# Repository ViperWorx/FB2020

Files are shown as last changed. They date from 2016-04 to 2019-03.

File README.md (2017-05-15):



<h3>Reliability, Speed, Accuracy, Open Source</h3>

This sums up the FB2020 CoreXY 3D Printer. We use these printers ourselves and wouldn’t sell the kits if we didn’t think they were up to snuff. Our FB2020s have run thousands of hours with very little down time. We print all the FB2020 printed parts on our FB2020s.

<h3>Reliability</h3>

The FB2020’s heart is the tried and trusted RAMPS 1.4 & Arduino Mega running the Marlin Firmware. It has tried and trusted A4988 Stepper Drivers moving the motors . With an AxMod 3D Print Drakon Geared extruder powering the filament through the bowden tube into a Genuine E3D v6 Hot end. This makes for a winning combination. The heated bed is a glass sheet heated by the tried and trusted Mk2B PCB heater. All of this adds up to a reliable printer.

<h3>Speed</h3>

With the 32 bit upgrade, replacing the Arduino Mega for a Re-Arm 32 Bit controller running Smoothieware, the FB2020 can handle 150mm/s speeds without skipping a beat. The standard Arduino Mega, being 8 bit, can handle speeds up to 80mm/s

<h3>Low Maintenance Accuracy</h3>

Running the E3D v6 and the Drakon Geared Extruder, it’s smooth printing. The FB2020 is capable of layer heights of 60 Microns up to 500 Microns and can print pretty much any filament you can throw at it. Adding a sheet of Printbite with the Basic bed upgrade allows for a low maintenance bed with great adhesion. The Full bed upgrade uses the same Printbite sheet on top of a laser cut 6061 5mm thick Aluminium bed heated by a SSR switched Mains heater. This speeds heat up times and allows bed temperatures of up to 130°c.  Upgrading the Drakon Extruder to a SLS version gives even more piece of mind for smooth running.

The Bill of Materials and further infomation can be found in the Wiki.

Firmware can be found at https://github.com/AxMod3DPrint/FB2020-Firmware

<hr />
<table border="0px">
<th align="left">
&copy; AxMod 3D Print 2017.
</th>
<tr>
<td>
This documentation describes Open Hardware and is licensed under the CERN OHL v. 1.2.
</td>
</tr>
<tr>
<td>
You may redistribute and modify this documentation under the terms of the
CERN OHL v.1.2. (http://ohwr.org/cernohl). This documentation is distributed
WITHOUT ANY EXPRESS OR IMPLIED WARRANTY, INCLUDING OF
MERCHANTABILITY, SATISFACTORY QUALITY AND FITNESS FOR A
PARTICULAR PURPOSE. Please see the CERN OHL v.1.2 for applicable
conditions
</td>
</tr>
</table>

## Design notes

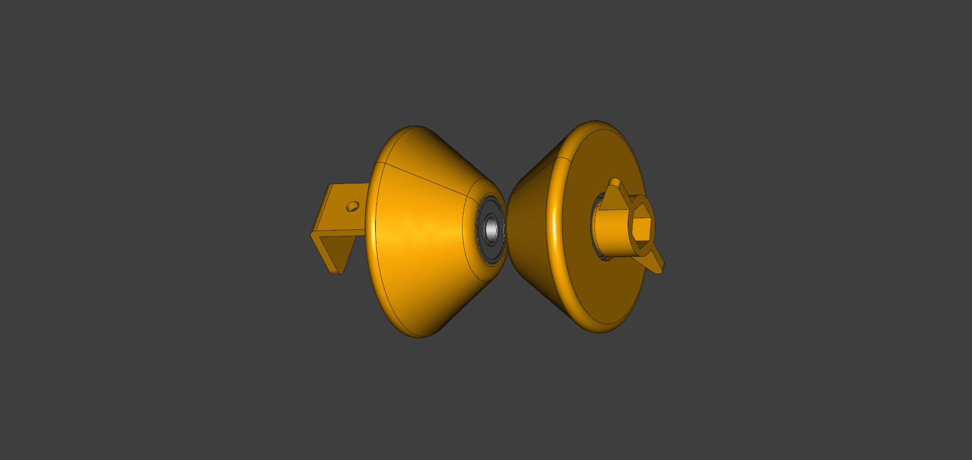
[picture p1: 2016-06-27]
Images/Spool Clamp_1.png

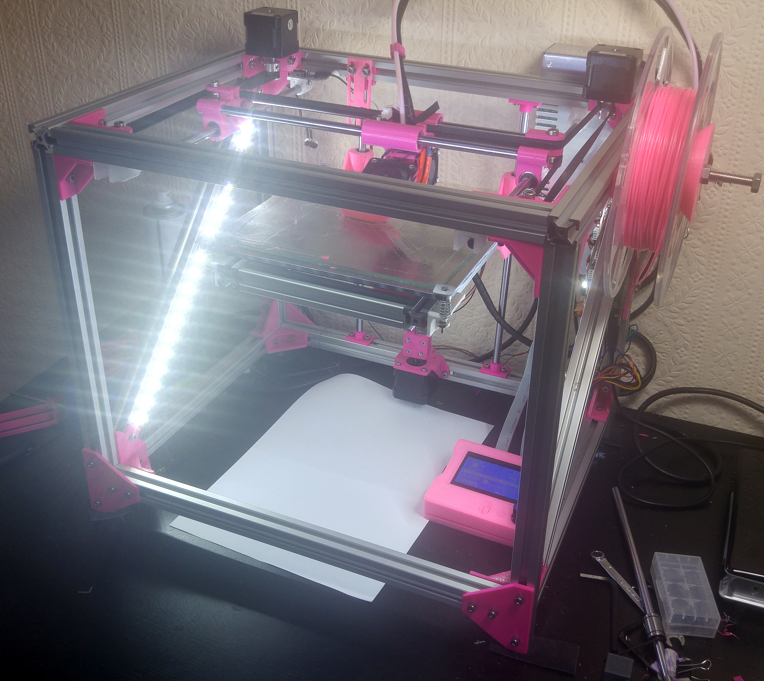
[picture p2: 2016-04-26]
Images/20160318_093008_HDR.jpg

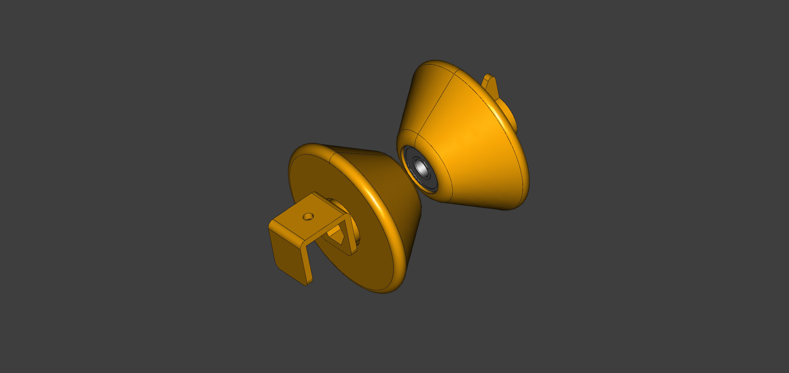
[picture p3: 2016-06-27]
Images/Spool Clamp_2.png

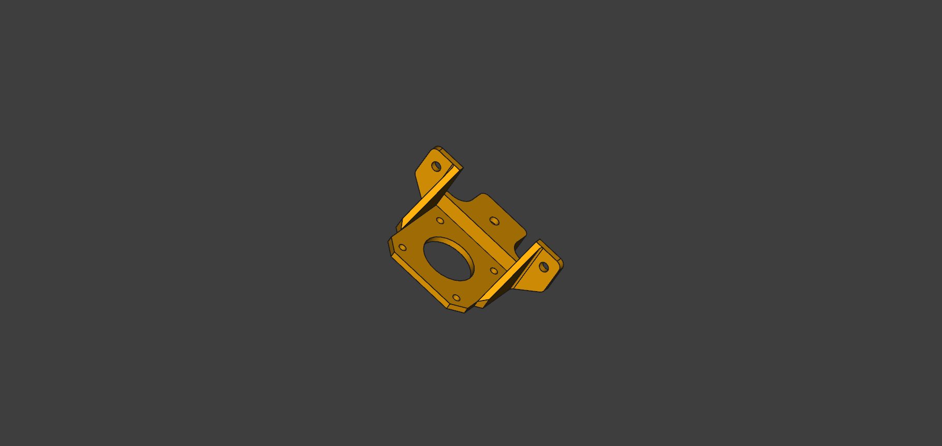
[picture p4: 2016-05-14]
Images/Z_Motor_Holder_1.png

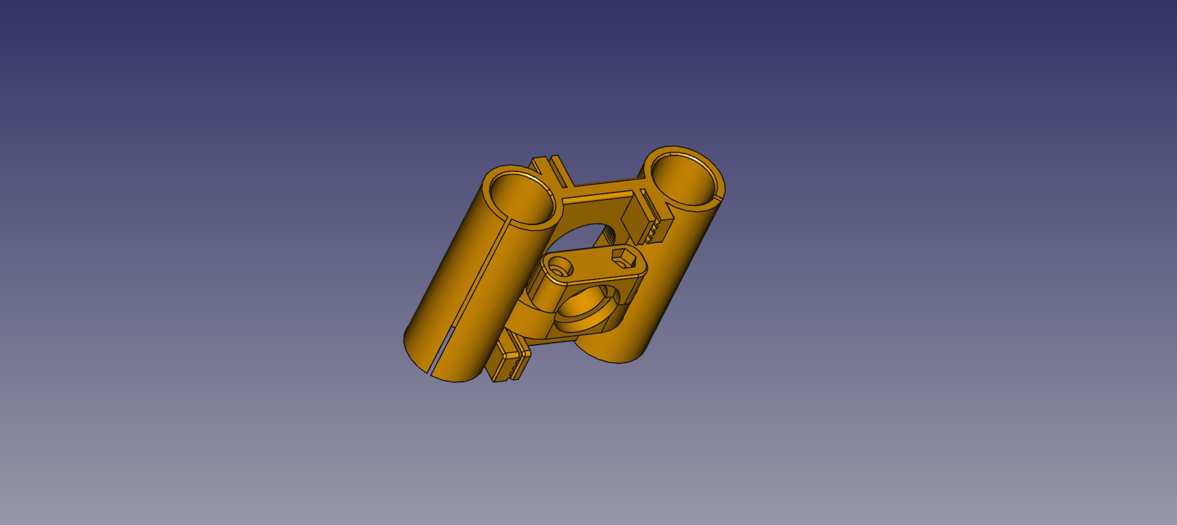
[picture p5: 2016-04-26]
Images/1_Carriage_freecad.png

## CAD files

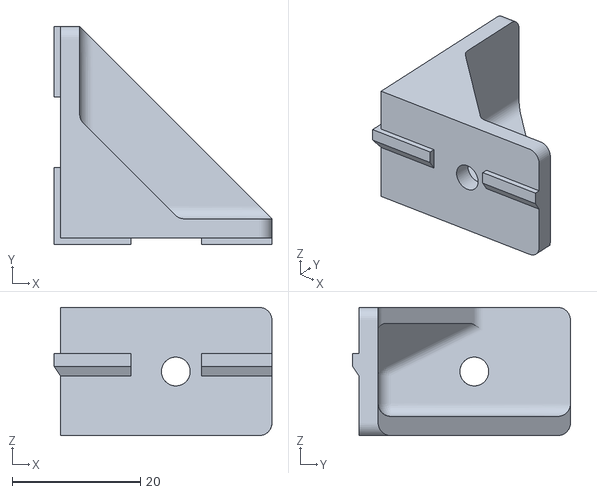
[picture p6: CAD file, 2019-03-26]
12_Corner_Bracket.stl
34.0 x 34.0 x 20.0

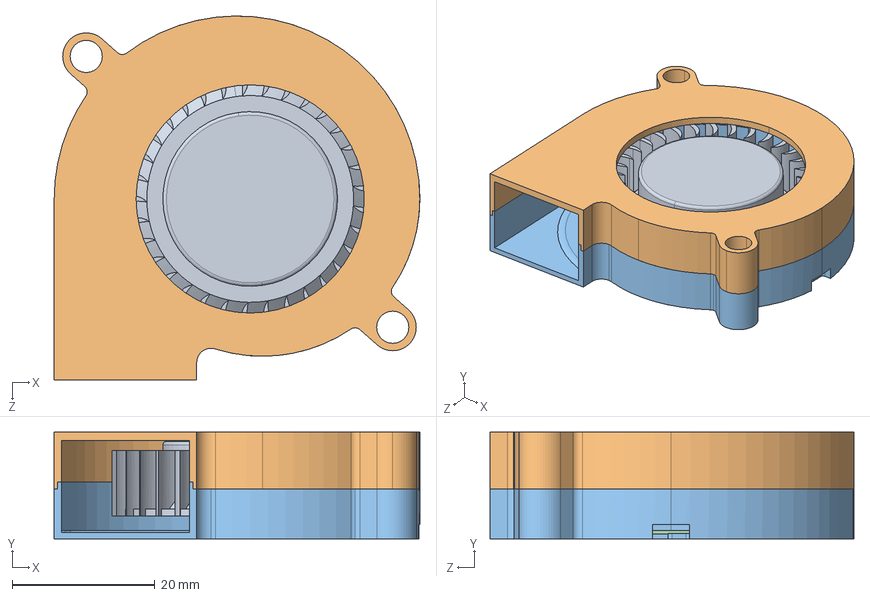
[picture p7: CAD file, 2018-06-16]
FreeCad/CAD Files/Radial-Cooling-Fan-5015-DC12V.STEP
51.3 x 15.0 x 51.1 mm
turbine
top
bottom

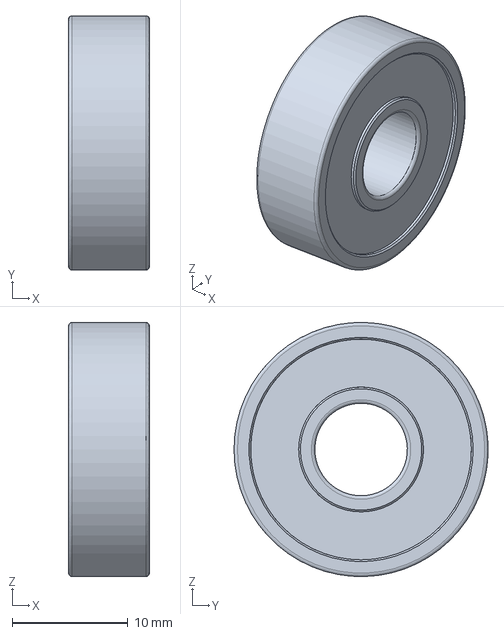
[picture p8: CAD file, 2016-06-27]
FreeCad/IGES/608ZZ.igs
7.00 x 22.0 x 22.0 mm

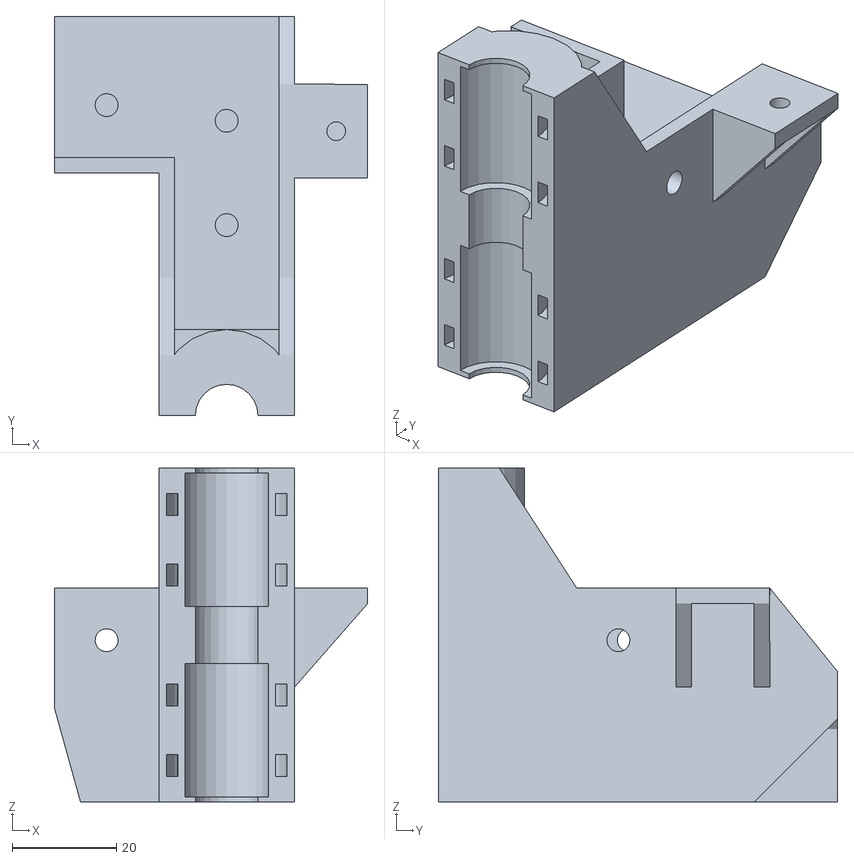
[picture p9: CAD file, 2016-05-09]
SCAD/Left_Bed_Holder_NEW.stl
60.0 x 76.5 x 64.0

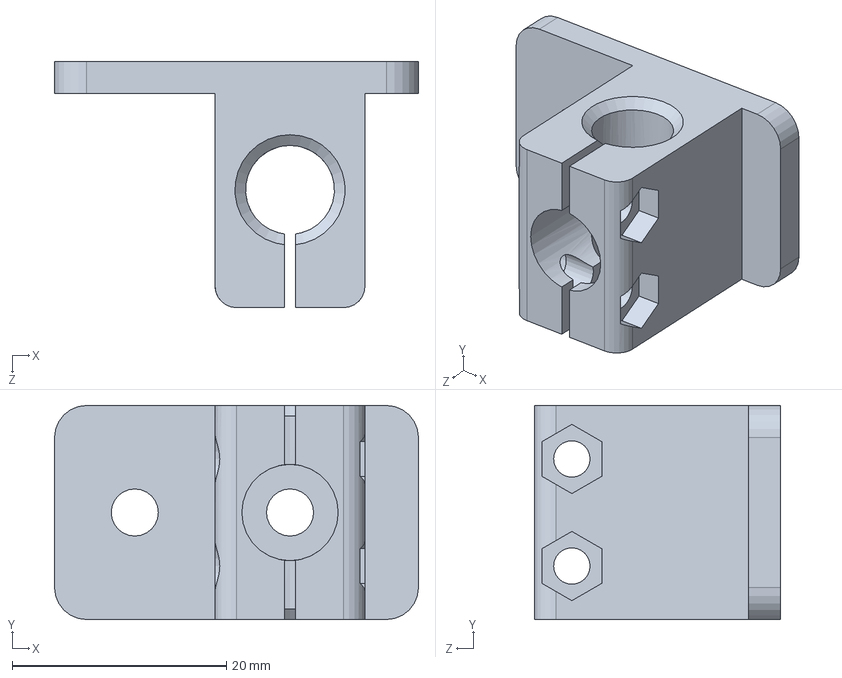
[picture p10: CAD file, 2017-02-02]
Solidworks/SW-2_Y_Rod_Holder_Left.SLDPRT
34.0 x 20.0 x 23.0 mm

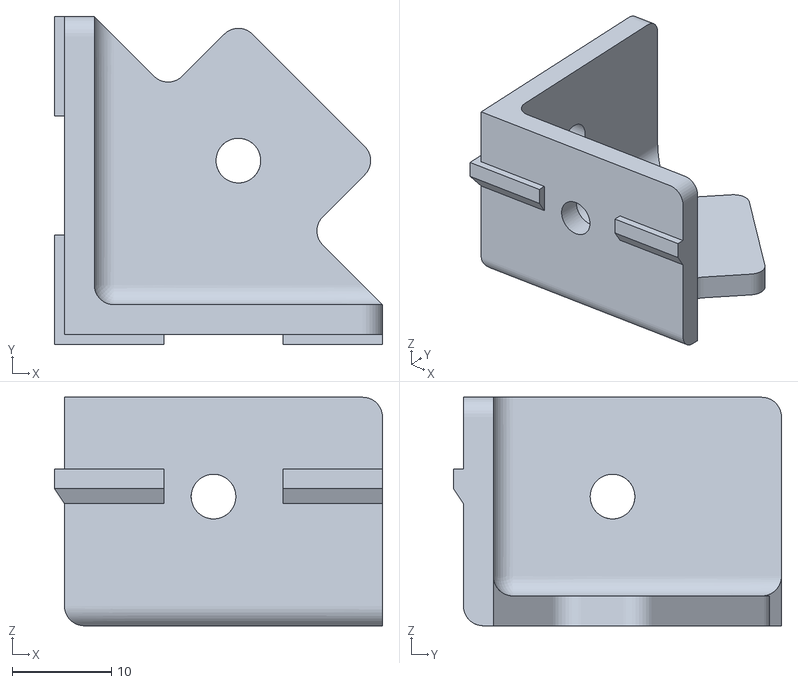
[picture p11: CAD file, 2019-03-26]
4_Corner_Brace_Mount.stl
33.0 x 33.0 x 23.0

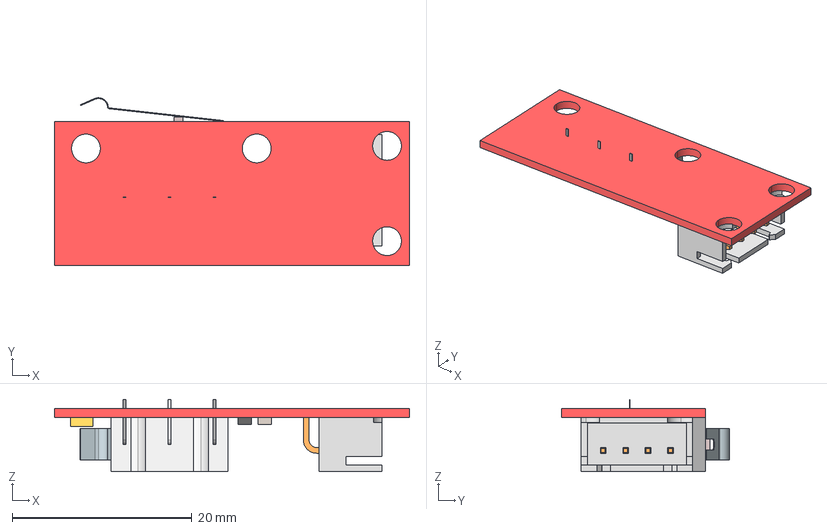
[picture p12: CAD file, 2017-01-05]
FreeCad/CAD Files/Endstop2.stp
39.5 x 18.6 x 8.02 mm
PCB Geometry
PCB^Endstop
Microswitch_1A_125vAC(seul)
JST 4Pin

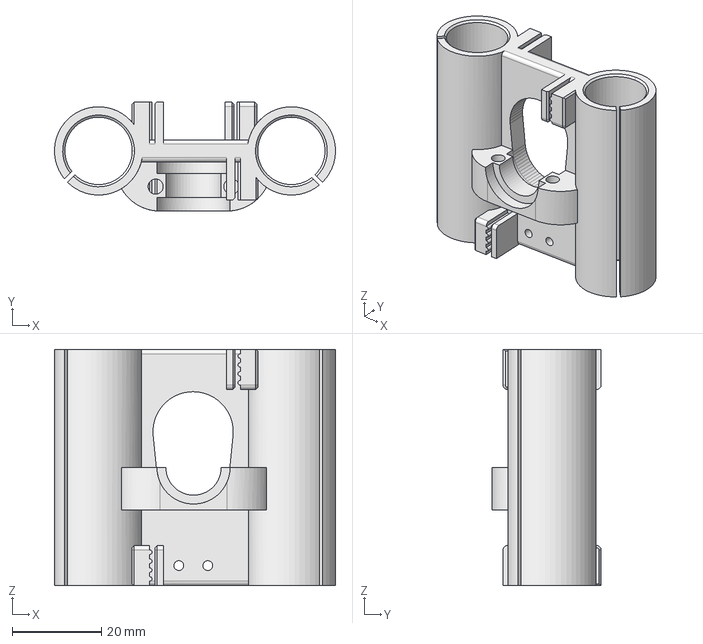
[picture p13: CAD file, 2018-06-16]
FreeCad/FB2020_Carriage.step
63.0 x 24.5 x 53.0 mm

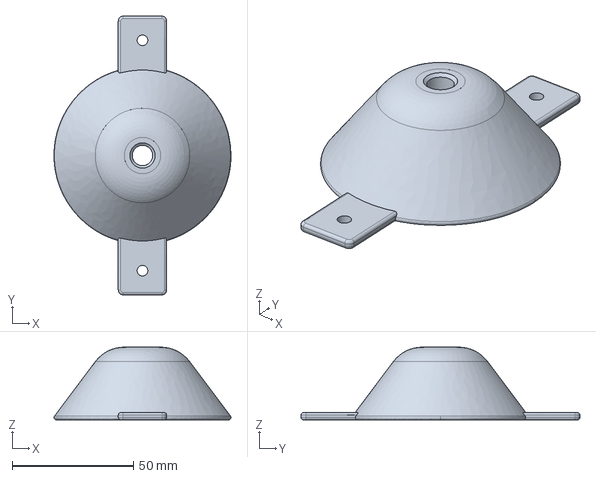
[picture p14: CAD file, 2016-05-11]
FreeCad/IGES/Spool_Clamp_Frame.iges
73.0 x 115.0 x 30.0 mm

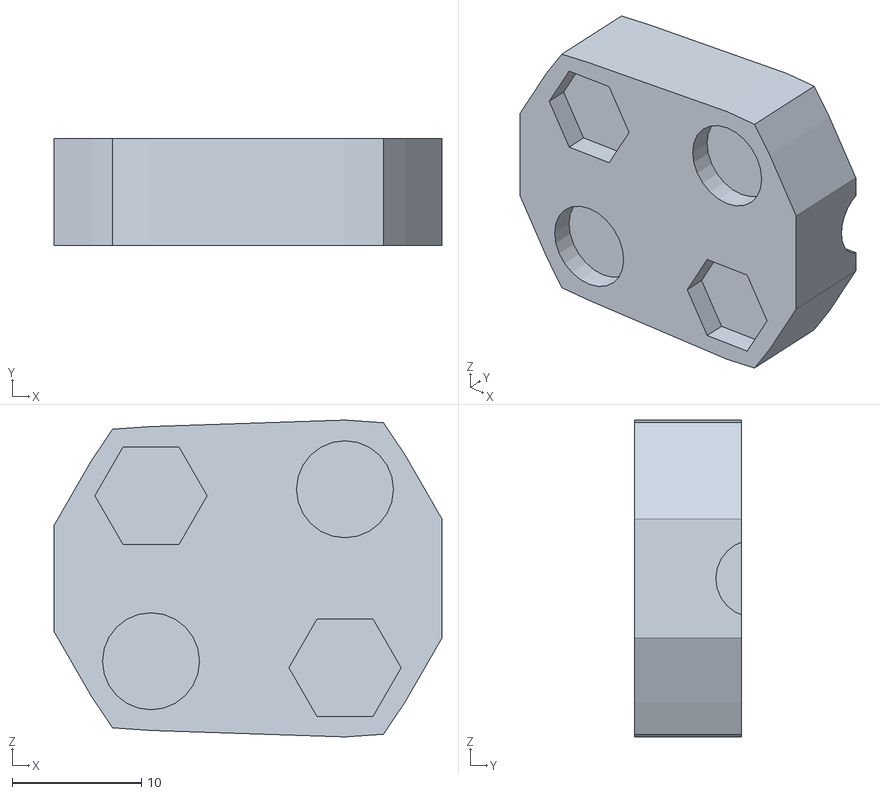
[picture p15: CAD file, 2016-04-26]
SCAD/coupler.stl
30.0 x 8.30 x 24.5

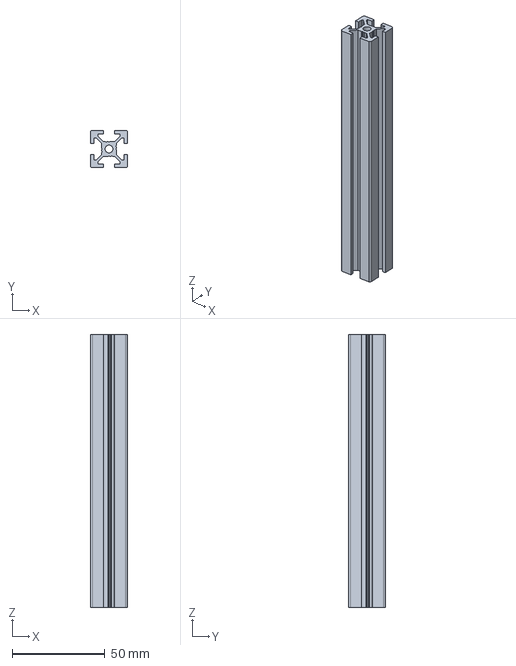
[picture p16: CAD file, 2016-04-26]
FreeCad/CAD Files/NFS5-2020-147_2_03.stp
20.0 x 20.0 x 147.0 mm

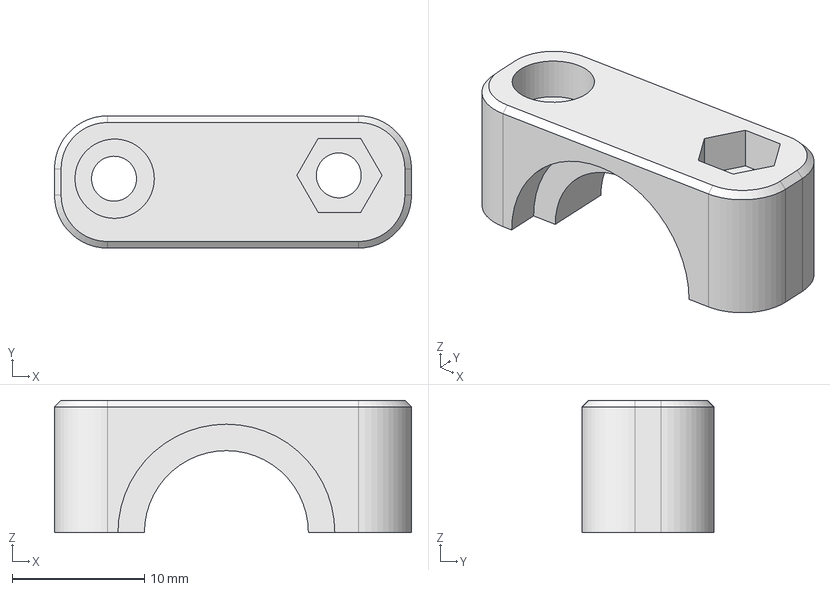
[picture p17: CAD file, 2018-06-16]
FreeCad/FB2020_Carriage_Clamp.step
27.0 x 10.0 x 10.0 mm

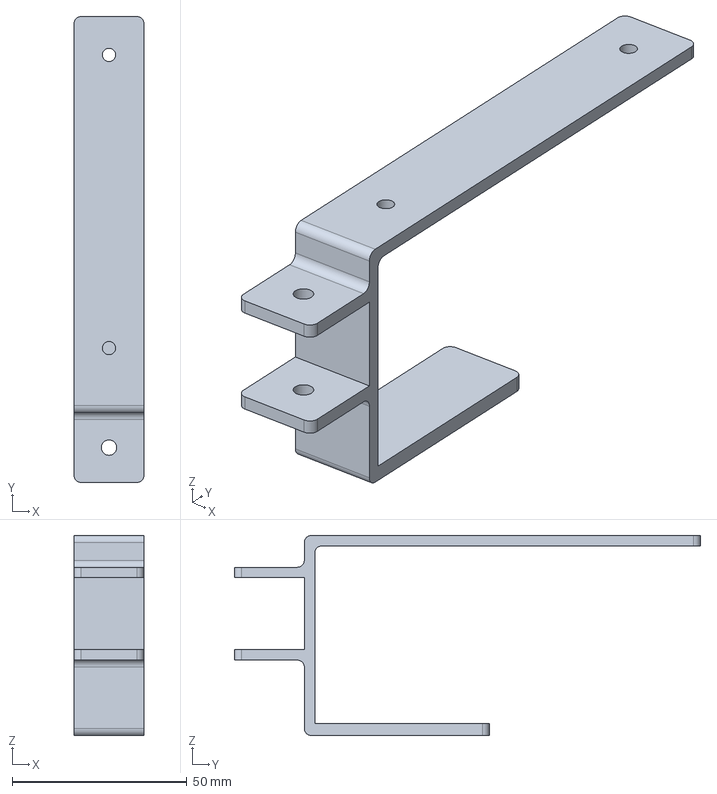
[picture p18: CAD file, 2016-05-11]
FreeCad/IGES/PSU_Mount_2.iges
20.0 x 133.5 x 57.3 mm

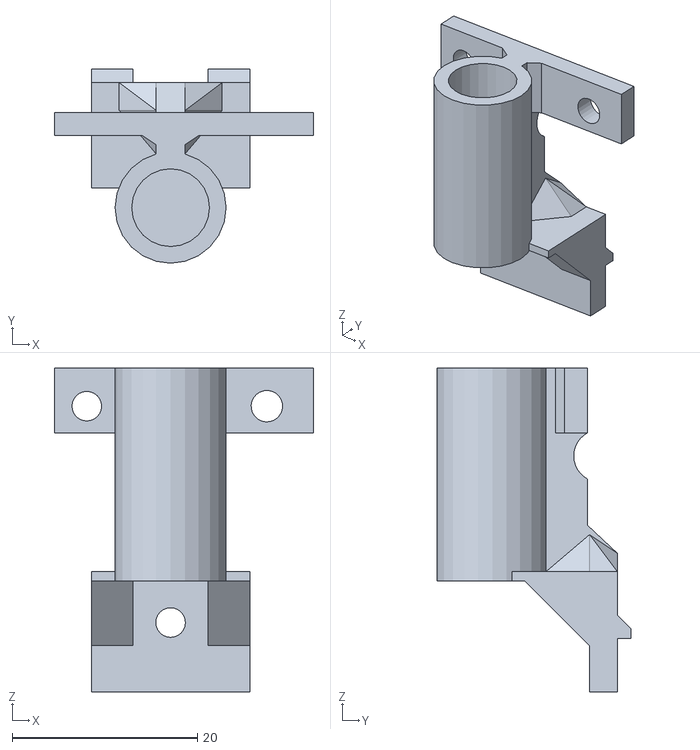
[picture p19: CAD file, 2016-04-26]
SCAD/rod_clamp_endstop.stl
28.0 x 21.0 x 35.0

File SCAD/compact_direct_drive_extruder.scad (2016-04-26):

// Compact direct drive bowden extruder for 1.75mm filament
// Licence: CC BY-SA 3.0, http://creativecommons.org/licenses/by-sa/3.0/
// Author: Dominik Scholz <schlotzz@schlotzz.com> and contributors
// Using MK8 style hobbed pulley 13x8mm from: https://www.reprapsource.com/en/show/6889
// visit: http://www.schlotzz.com
// changed: 2014-04-04, added idler slot and funnel on bowden side for easier filament insertion
// changed: 2014-04-27, placed base and idler "printer ready"
// changed: 2014-09-22, fixed non-manifold vertexes between base and filament tunnel
// changed: 2014-11-13, added bowden inlet
// changed: 2015-03-17, updated idler for better MK7 drive gear support
// changed: 2015-10-13, designed alternative idler to solve breaking of bearing support


/*
	design goals:
	- use 13x8mm hobbed pulley (mk8) or 13x12mm (mk7)
	- filament diameter parametric (1.75mm or 3mm)
	- use 608zz bearing
	- use M5 push fit connector
*/

// avoid openscad artefacts in preview
epsilon = 0.01;

// increase this if your slicer or printer make holes too tight
extra_radius = 0.2;

// major diameter of metric 3mm thread
m3_major = 2.85;
m3_radius = m3_major / 2 + extra_radius;
m3_wide_radius = m3_major / 2 + extra_radius + 0.2;

// diameter of metric 3mm hexnut screw head
m3_head_radius = 3 + extra_radius;

// drive gear
drive_gear_outer_radius = 8.00 / 2;
drive_gear_hobbed_radius = 7 / 2;
drive_gear_hobbed_offset = 3.5;
drive_gear_length = 13.5;
drive_gear_tooth_depth = 0.5;

// base width for frame plate
base_width = 20;
base_length = 62;
base_height = 5;

// nema 17 dimensions
nema17_width = 42.3;
nema17_hole_offsets = [
	[-15.5, -15.5, 1.5],
	[-15.5,  15.5, 1.5],
	[ 15.5, -15.5, 1.5],
	[ 15.5,  15.5, 1.5 + base_height]
];

// inlet type
inlet_type = 0; // 0:normal, 1:push-fit


// filament
filament_diameter = 1.75; // 1.75, 3.00
filament_offset = [
	drive_gear_hobbed_radius + filament_diameter / 2 - drive_gear_tooth_depth,
	0,
	base_height + drive_gear_length - drive_gear_hobbed_offset - 2.5
];





// helper function to render a rounded slot
module rounded_slot(r = 1, h = 1, l = 0, center = false)
{
	hull()
	{
		translate([0, -l / 2, 0])
			cylinder(r = r, h = h, center = center);
		translate([0, l / 2, 0])
			cylinder(r = r, h = h, center = center);
	}
}


// mounting plate for nema 17
module nema17_mount()
{
	// settings
	width = nema17_width;
	height = base_height;
	edge_radius = 27;
	axle_radius = drive_gear_outer_radius + 1 + extra_radius;

	difference()
	{
		// base plate
		translate([0, 0, height / 2])
			intersection()
			{
				cube([width, width, height], center = true);
				cylinder(r = edge_radius, h = height + 2 * epsilon, $fn = 128, center = true);
			}
		
		// center hole
		translate([0, 0, -epsilon]	)
			cylinder(r = 11.25 + extra_radius, h = base_height + 2 * epsilon, $fn = 32);

		// axle hole
		translate([0, 0, -epsilon])
			cylinder(r = axle_radius, h = height + 2 * epsilon, $fn = 32);

		// mounting holes
		for (a = nema17_hole_offsets)
			translate(a)
			{
				cylinder(r = m3_radius, h = height * 4, center = true, $fn = 16);
				cylinder(r = m3_head_radius, h = height + epsilon, $fn = 16);
			}
	}
}


// plate for mounting extruder on frame
module frame_mount()
{
	// settings
	width = base_width;
	length = base_length;
	height = base_height;
	hole_offsets = [
		[0,  length / 2 - 6, 2.5],
		[0, -length / 2 + 6, 2.5]
	];
	corner_radius = 3;

	difference()
	{
		// base plate
		intersection()
		{
			union()
			{
				translate([0, 0, height / 2])
					cube([width, length, height], center = true);
				translate([base_width / 2 - base_height / 2 - corner_radius / 2, 0, height + corner_radius / 2])
					cube([base_height + corner_radius, nema17_width, corner_radius], center = true);
				translate([base_width / 2 - base_height / 2, 0, 6])
					cube([base_height, nema17_width, 12], center = true);
			}

			cylinder(r = base_length / 2, h = 100, $fn = 32);
		}

		// rounded corner
		translate([base_width / 2 - base_height - corner_radius, 0, height + corner_radius])
			rotate([90, 0, 0])
				cylinder(r = corner_radius, h = nema17_width + 2 * epsilon, center = true, $fn = 32);

		// mounting holes
		for (a = hole_offsets)
			translate(a)
			{
				cylinder(r = m3_wide_radius, h = height * 2 + 2 * epsilon, center = true, $fn = 16);
				cylinder(r = m3_head_radius, h = height + epsilon, $fn = 16);
			}

		// nema17 mounting holes
		translate([base_width / 2, 0, nema17_width / 2 + base_height])
			rotate([0, -90, 0])
			for (a = nema17_hole_offsets)
				translate(a)
				{
					cylinder(r = m3_radius, h = height * 4, center = true, $fn = 16);
					cylinder(r = m3_head_radius, h = height + epsilon, $fn = 16);
				}
	}
}


// inlet for filament
module filament_tunnel()
{
	// settings
	width = 9;
	length = nema17_width;
	height = filament_offset[2] - base_height + 4.5;

	translate([0, 0, height / 2])
	{
		difference()
		{
			union()
			{
				// base
				translate([-height / 2, 0, 0])
					cube([width + height, length, height], center = true);

				// inlet strengthening
				translate([0, -length / 2, -height / 2 + filament_offset[2] - base_height])
					rotate([90, 0, 0])
						cylinder(r = 3.5, h = 1, center = true, $fn = 32);

				// outlet strengthening
				translate([0, length / 2, -height / 2 + filament_offset[2] - base_height])
					rotate([90, 0, 0])
						cylinder(r = 4.5, h = 1, center = true, $fn = 32);

				// idler tensioner
				intersection()
				{
					translate([5, -length / 2 + 8, 0])
						cube([width, 16, height], center = true);
					translate([-17.8, -20 ,0])
						cylinder(r = 26.5, h = height + 2 * epsilon, center = true, $fn = 32);
				}

			}

			// middle cutout for drive gear
			translate([-filament_offset[0], 0, 0])
				cylinder(r = 11.25 + extra_radius, h = height + 2 * epsilon, center = true, $fn = 32);

			// middle cutout for idler
			translate([11 + filament_diameter / 2, 0, 0])
				cylinder(r = 12.5, h = height + 2 * epsilon, center = true, $fn = 32);

			// idler mounting hexnut
			translate([filament_diameter + 1, -nema17_width / 2 + 4, .25])
				rotate([0, 90, 0])
					cylinder(r = m3_radius, h = 50, center = false, $fn = 32);
			translate([filament_diameter + 3, -nema17_width / 2 + 4, 5])
				cube([2.5 + 3 * extra_radius, 5.5 + 2.5 * extra_radius, 10], center = true);
			translate([filament_diameter + 3, -nema17_width / 2 + 4, 0])
				rotate([0, 90, 0])
					cylinder(r = 3.15 + 2.5 * extra_radius, h = 2.5 + 3 * extra_radius, center = true, $fn = 6);
			
			// rounded corner
			translate([-height - width / 2, 0, height / 2])
				rotate([90, 0, 0])
					cylinder(r = height, h = length + 2 * epsilon, center = true, $fn = 32);
			
			// funnnel inlet
			if (inlet_type == 0)
			{
				// normal type
				translate([0, -length / 2 + 1 - epsilon, -height / 2 + filament_offset[2] - base_height])
					rotate([90, 0, 0])
						cylinder(r1 = filament_diameter / 2, r2 = filament_diameter / 2 + 1 + epsilon / 1.554,
							h = 3 + epsilon, center = true, $fn = 16);
			}
			else
			{
				// inlet push fit connector m5 hole
				translate([0, -length / 2 - 1 + 2.5 + epsilon, -height / 2 + filament_offset[2] - base_height])
					rotate([90, 0, 0])
						cylinder(r = 2.25, h = 5 + 2 * epsilon, center = true, $fn = 16);

				// funnel inlet outside
				translate([0, -length / 2 + 4, -height / 2 + filament_offset[2] - base_height])
					rotate([90, 0, 0])
						cylinder(r1 = filament_diameter / 2, r2 = filament_diameter / 2 + 1,
							h = 2, center = true, $fn = 16);

			}

			// funnnel outlet inside
			translate([0, 12, -height / 2 + filament_offset[2] - base_height])
				rotate([90, 0, 0])
					cylinder(r1 = filament_diameter / 2, r2 = filament_diameter / 2 + 1.25,
						h = 8, center = true, $fn = 16);

			// outlet push fit connector m6 hole
			translate([0, length / 2 + 1 - 2.5 + epsilon, -height / 2 + filament_offset[2] - base_height])
				rotate([90, 0, 0])
					cylinder(r = 2.8, h = 5 + 2 * epsilon, center = true, $fn = 16);

			// funnel outlet outside
			translate([0, length / 2 - 4, -height / 2 + filament_offset[2] - base_height])
				rotate([90, 0, 0])
					cylinder(r1 = filament_diameter / 2 + 1, r2 = filament_diameter / 2,
						h = 2, center = true, $fn = 16);

			// filament path
			translate([0, 0, -height / 2 + filament_offset[2] - base_height])
				rotate([90, 0, 0])
					cylinder(r = filament_diameter / 2 + 2 * extra_radius,
						h = length + 2 * epsilon, center = true, $fn = 16);
			
			// screw head inlet
			translate(nema17_hole_offsets[2] - [filament_offset[0], 0, height / 2 + 1.5])
				sphere(r = m3_head_radius, $fn = 16);
		}
	}
}


// render drive gear
module drive_gear()
{
	r = drive_gear_outer_radius - drive_gear_hobbed_radius;
	rotate_extrude(convexity = 10)
	{
		difference()
		{
			square([drive_gear_outer_radius, drive_gear_length]);
			translate([drive_gear_hobbed_radius + r, drive_gear_length - drive_gear_hobbed_offset])
				circle(r = r, $fn = 16);
		}
	}
}
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

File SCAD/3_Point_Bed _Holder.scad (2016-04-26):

$fn=64;
difference(){
cube([40,20,3]);
translate([8,10,-1])
cylinder(d=4.2,h=5);
translate([35,10,-1])
cylinder(d=4.2,h=5);
}
difference(){
cube([40,3,15]);
translate([20.5,4,10.5])
rotate([90,0,0])
cylinder(d=3.4,h=5);
}
difference(){
cube([3,20,15]);
translate([-1,2,16])
rotate(a=34, v=[-1,0,0])
cube([5,25,20]);
}


difference(){
translate([40,0,0])
cube([3,20,15]);
translate([39,2,16.05])
rotate(a=34, v=[-1,0,0])
cube([5,25,20]);
}

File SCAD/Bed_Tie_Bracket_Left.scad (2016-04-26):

$fn=64;



module stiffening(){
translate([2.5,2.5,0])
cylinder(d=5, h=35);
translate([0,2.5,2.5])
rotate([0,90,0])
cylinder(d=5, h=26);
translate([2.5,0,2.5])
rotate([-90,0,0])
cylinder(d=5, h=20);
}

difference(){
cube([26,20,3]);
translate([13,10,-1])
cylinder(d=4.4, h=5);
}


difference(){
cube([3,20,35]);
translate([-1,10,10])
rotate([0,90,0])
cylinder(d=4.4, h=5);
translate([-1,10,28])
rotate([0,90,0])
cylinder(d=4.4, h=5);
}
difference(){
cube([26,3,35]);
translate([26,-1,5])
rotate([0,-35,0])
cube([20,5,50]);
}
stiffening();

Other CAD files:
Solidworks/SW-2_Y_Rod_Holder_Right.SLDPRT
Solidworks/SW-1_RRD_Case_Button.SLDPRT
1_Carriage_E3D_Threaded_Heatsink.stl
FreeCad/CAD Files/NFS5-2020-340_2_03.stp
SCAD/Bed _Holder.scad
1_12mm_Bed_Carrier_Left.stl
1_12mm_Bed_Carrier_Right.stl
1_30mm_Fan_Guard.stl
1_3_Point_Bed _Holder.stl
1_Bed_Tie_Bracket_Left.stl
1_Bed_Tie_Bracket_Right.stl
1_Bowden_Clip.stl
1_Carriage.stl
1_Carriage_clamp.stl
1_Carrier_Left.stl
1_Carrier_Right.stl
1_Compact_Direct_Drive_Extruder.stl
1_E3D_duct_small.stl
1_Extruder_Spring_Holder.stl
1_Left_Bed_Holder_Clamp_Short.stl
1_Left_Bed_Holder_clamp.stl
1_Left_Idler_Corner.stl
1_MKS_Base_Mount.stl
1_PSU_Mount_1_S-200-12.stl
1_PSU_Mount_2_S-200-12.stl
1_RAMPS_Box_Base.stl
1_RAMPS_Box_Lid.stl
1_RAMPS_Box_Reset_Button.stl
1_RAMPS_Mount.stl
1_RRD_Case Front.stl
1_RRD_Case_Back.stl
1_RRD_Case_Button.stl
1_RRD_Knob.stl
1_RRD_Knob_15mm.stl
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

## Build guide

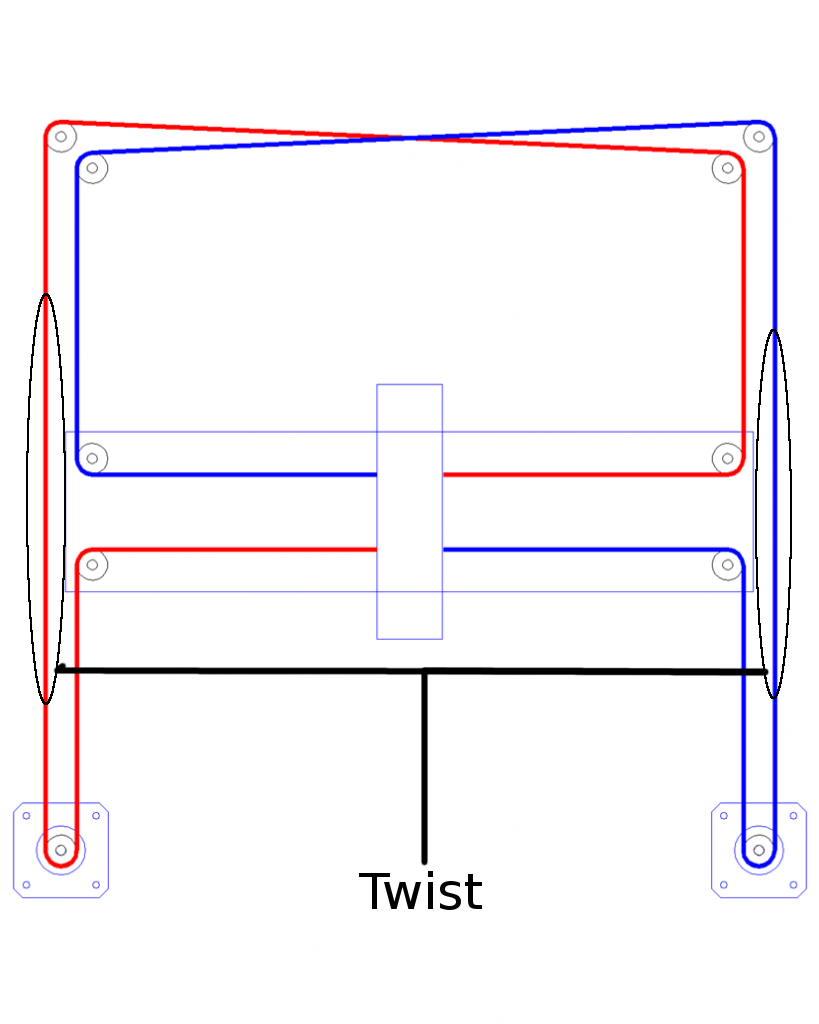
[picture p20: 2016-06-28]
Build Guide/Images/Belt Path2.png

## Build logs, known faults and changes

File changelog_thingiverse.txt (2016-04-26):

#####02/02/16

original upload

#####03/02/16

Bed Mounts uploaded

#####04/02/16

Rigid coupler added

#####05/02/16

Rigid Coupler design slimmed down (damn my spacial awareness), Carriage modified to stiffen up clamp for E3D

#####06/02/16

Carriage modified to allow for printing without supports, clamp shortened by 2mm

#####07/02/16

Bed Holder bearing holes enlarged by 0.3mm to allow easier fitting of the bearings and to allow for printing variances. Carriage SCAD file & RAMPS mount uploaded

#####09/02/16

Modified Z Leadscrew Holder & Z Endstop mount - original had holes too close for T nuts.

#####14/02/15

Added quick and dirty spool clamp. Needs M8 Threaded rod and 2 13mm nuts

#####16/02/15

Added carriers for Y axis. Designed to work with the new X Carriage as the belt clips will not align with the existing Carriers. Uploaded all parts. Carriers printed and found to be a little tight on the bearings and not enough space to guide the belts. Modified to guide the belts, left carrier now has endstop lug to hit the Y endstop.

#####18/02/15

Reinforced Y rod carriers, fed up of them breaking. Carrier near right hand idler will need support. Printed and modified again (removed cap our rail mounts) to allow for irregular length rods. Mine are ~1mm out. Carriers modified to allow the same. Bill of Materials added

#####20/02/15

Carriage modified, reinforcing belt clips fixed bearing alignment with carriers. Bed Carrier extrusion slots widened by 0.4mm. Far too tight to fit the bed extrusions effectively.

#####25/02/15

Left and Right Carriers now have inbuilt support on the clamp slot, this was done due to printing issues. Extruder Carriage now has slightly thicker and taller belt clips. Spool holder nut slot enlarged due to being too small. Short version of the Z axis Carriers added, allows use of LM8LUUs. Removed rigid coupler as there's a slight Z wobble. Leadscrew nut holder central hole increased in size as too small. All files refreshed and have been numbered with the amount to print. Lost spool holder SCAD file in a shift-delete accident.. :(. Files marked Culain are originals from Culain's design. The bed holders have just been re-orientated and mirrored, no other physical changes have been made. After a conversation over on the RepRap forums, the option to add an endstop to the Extruder Carriage has been added. You will need a standard Omron style micro-switch and 2x 14mm M2 bolts, these should screw directly into the Carriage but can alst use nuts on the other side. This allows one bundle of cables and tubing to be moving over having the endstop moving on the Y Axis and the Bowden tube moving on the Carriage. Derped on hole placement for Omron Microswitch, corrected. Moved Y endstop bumper down, wouldn't make proper contact. Uploaded SCAD files for Carriers and Spool Clamp, didn't delete it after all.

#####27/02/16

Added Left carrier with no endstop mount to complement the move of the endstop to the carriage - this will print without support, STL & SCAD file uploaded for this. Updated RAMPS mount, Derped putting stand-offs on the wrong side. Moved the RAMPS in by 5mm

#####03/03/16

Front Bed Holders reworked as they did not fit. Corner Idlers strengthened, the top bearing holder was constantly breaking on the right side. Z Endstop mount lengthened due to not enough travel. Renamed FB2020 due to very little being left of the original design and is now in it's own right a different printer. Added Bowden Tube wire clips, source added.

#####06/03/16

Z Endstop reworked, now uses an Omron-style limit switch and bumps off of the Z Carrier. Fron Bed Tie added to stiffen up bed, (this can be changed out for another 147mm Extrusion piece and 2 more corner brackets. Front bed holders tweaked to bring holes in line with the Z Axis bed holders. Added a new Rigid Coupler for the Z Axis, clamps concentrically with 2x M3x16 Bolts. Z Leadscrew length shortened to 250mm as 300mm fouls the Extruder carriage

#####08/03/15

Carriage - Belt clip notches moved to opposite side and E3D mount widened to allow easy fitting - SCAD file modified to allow extra diameter for printing. A twist in the Belts on the outer long runs is now needed. This makes the belt run on the smooth side for all the idlers and increases print quality.

Idlers - Re-orientated for strength layers are now in the opposite direction of the belt tension, now need printing with support.

Bowden tube wire clips added to keep Bowden tube and hot end wiring together and tidy

Bowden Clip added to keep E3D collet up and stop filament backlash.

Compact Direct Drive Extruder added - modified for a 6mm Pneumatic Coupler and an E3D HobbGoblin Drive Gear

Updated BOM to reflect changes.

#####02/04/16

Firmware updated to Marlin 1.1 RC4. Enabled Mesh Bed Levelling and PID on the Bed. X0 Y0 is the Front left of the printer, Y homes to Max.

#####07/04/16

Changed layer fan for spinorkit's 2 pronged setup, which has been shortened to allow clearance of the leadscrew, this layer fan assembly is a lot more effective as it cools from two sides. As such this needed a new Active cooling duct for the E3D hot end, to mount the layer fan off of, this cooling duct clamps with 2 22mm M3 bolts and will not move once clamped.

#####14/04/16

Description updated and planned changes added.

#####17/04/16

Bed converted to 3 point levelling, new brackets added, use front bed tie for the middle of the bed to stiffen. Longer lengths for bed reduced to 235mm.

#####19/04/16

Carriage updated. Added extra room for cabling from hot end & flattened off clamp on carriage. This should allow for easier belt fitting and will retain the nut on the clamp on the carriage. Several minor changes including centring up of the hot end. Note the STLS are uploaded with 0.4mm tolerance as my Prusas print tight. If you need less grab the SCAD file.

#####20/04/16

Carriage extended by 5mm to allow further easier fitting of belts and hot end. There's roughly 4.5mm either side of the bed so there is room for further extension if needed.

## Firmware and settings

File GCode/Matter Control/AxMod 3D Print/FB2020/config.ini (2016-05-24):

avoid_crossing_perimeters = 1
bed_shape = rectangular
bed_size = 200,200
bed_temperature = 60
bottom_clip_amount = 0
bridge_acceleration = 0
bridge_fan_speed = 100
bridge_flow_ratio = 1
bridge_speed = 20
brim_width = 0
build_height = 170
cancel_gcode = 
center_part_on_bed = 1
complete_objects = 0
cool_extruder_lift = 0
cooling = 1
create_raft = 0
default_acceleration = 0
disable_fan_first_layers = 1
end_gcode = M140 S0 T0; set bed temperature to 0\nM104 S0 T0; set extruder temperature to 0\nM107 ; disable fan\nG91 ;Relative positioning\nG1 E-1 F300  ;retract the filament a bit before lifting the nozzle to release some of the pressure\nG1 E-5 F4800; Retract\nG90 ; Absolute positioning\nG1 Z275; Bed to bottom of printer\nG28 X Y F4800; home X & Y axis\nM84; disable all stepper motors\nM117 Work Complete!end_gcode = M140 S0 T0; set bed temperature to 0\nM104 S0 T0; set extruder temperature to 0\nM107 ; disable fan\nG91 ;Relative positioning\nG1 E-1 F300  ;retract the filament a bit before lifting the nozzle to release some of the pressure\nG1 E-5 F4800; Retract\nG90 ; Absolute positioning\nG1 Z275; Bed to bottom of printer\nG28 X Y F4800; home X & Y axis\nM84; disable all stepper motors\nM117 Work Complete!
external_perimeter_speed = 50%
external_perimeters_first = 0
extra_perimeters = 1
extruder_clearance_height = 20
extruder_clearance_radius = 20
extruder_count = 1
extruder_offset = 0x0,0x0,0x0,0x0
extruders_share_temperature = 0
extrusion_axis = E
extrusion_multiplier = 1
extrusion_width = 0
fan_always_on = 0
fan_below_layer_time = 60
filament_diameter = 1.75
fill_angle = 45
fill_density = 30%
fill_pattern = honeycomb
first_layer_acceleration = 0
first_layer_bed_temperature = 75
first_layer_height = 90%
first_layer_speed = 30%
first_layer_temperature = 205
g0 = 0
gap_fill_speed = 20
gcode_arcs = 0
gcode_comments = 0
gcode_flavor = reprap
gcode_output_type = REPRAP
has_fan = 1
has_hardware_leveling = 0
has_heated_bed = 1
has_sd_card_reader = 1
heat_extruder_before_homing = 0
infill_acceleration = 0
infill_every_layers = 1
infill_extruder = 1
infill_extrusion_width = 0
infill_first = 0
infill_only_where_needed = 0
infill_overlap_perimeter = .06
infill_speed = 50
infill_type = GRID
layer_gcode = 
layer_height = 0.2
max_fan_speed = 100
min_extrusion_before_retract = .1
min_fan_speed = 35
min_print_speed = 10
min_skirt_length = 0
notes = 
nozzle_diameter = 0.4
only_retract_when_crossing_perimeters = 1
ooze_prevention = 0
output_filename_format = [input_filename_base].gcode
overhangs = 1
pause_gcode = 
perimeter_acceleration = 0
perimeter_extruder = 1
perimeter_extrusion_width = 0
perimeter_speed = 30
perimeters = 3
post_process = 
print_center = 100,100
raft_air_gap = .2
raft_extruder = 0
raft_extra_distance_around_part = 5
raft_fan_speed_percent = 100
raft_layers = 0
raft_print_speed = 100%
randomize_start = 0
repair_outlines_extensive_stitching = 0
repair_outlines_keep_open = 0
resolution = 0
resume_gcode = 
retract_before_travel = 20
retract_layer_change = 1
retract_length = 6.4
retract_length_tool_change = 10
retract_lift = 0.2
retract_restart_extra = 0
retract_restart_extra_toolchange = 0
retract_speed = 30
skirt_distance = 6
skirt_height = 1
skirts = 3
slowdown_below_layer_time = 30
small_perimeter_speed = 30
solid_fill_pattern = rectilinear
solid_infill_below_area = 70
solid_infill_every_layers = 0
solid_infill_extrusion_width = 0
solid_infill_speed = 60
spiral_vase = 0
standby_temperature_delta = -5
start_gcode = G21 ; mm\nG90; Absolute Pos\nM107; Fan off\nG28; home all\nG92 E0 ;Zero Extruder\nG1 Z0.3 ;Move Z to 0.3mm to avoid scraping bed\nG1 X100 Y5 F4000 ;Move to half way along front edge of the bed\nG1 Z0.05 ;Move Nozzle close to bed\nG1 E10 F90 ; Extrude 10mm \nG1 X20 F120000; move to X20 as fast as firmware permits\nG1 Z2 ; Lift nozzle to 2mm ready to start main sequence\nG92 E0 ;Zero Extruder
start_perimeters_at_concave_points = 0
start_perimeters_at_non_overhang = 0
support_material = 0
support_material_angle = 45
support_material_enforce_layers = 0
support_material_extruder = 1
support_material_extrusion_width = 0
support_material_infill_angle = 45
support_material_interface_extruder = 1
support_material_interface_layers = 3
support_material_interface_spacing = 0
support_material_pattern = honeycomb
support_material_spacing = 2.5
support_material_speed = 50
support_material_threshold = 0
support_material_xy_distance = 0.7
support_material_z_distance = 0.15
support_material_z_gap_layers = 1
support_type = LINES
temperature = 200
thin_walls = 1
threads = 2
toolchange_gcode = 
top_infill_extrusion_width = 0
top_solid_infill_speed = 50
top_solid_layers = 3
travel_speed = 110
use_firmware_retraction = 0
use_relative_e_distances = 0
vibration_limit = 0
wipe = 1
wipe_shield_distance = 0
wipe_tower_size = 0
z_can_be_negative = 0
z_offset = 0

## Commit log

2016-04-26 Redesign of Z rod holder
    [4_Z_Rod_Mount.stl, Z_Rod_Holder.fcstd]
2016-04-26 mv old rod holder to old files
    [4_Z_Rod_Mount_Culain.stl]
2016-04-26 Made Z Rod Holder larger with more support around the base
    [4_Z_Rod_Mount.stl, Z_Rod_Holder.fcstd]
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2016-04-27 Full CAD design updated Filament loading GCode length reduced.
    [FB2020.fcstd]
2016-04-27 Extruder mounts converter to M4
    [1_Compact_Direct_Drive_Extruder.stl, 1_Compact_Direct_Drive_Extruder_M4.stl]
2016-04-27 printed T nuts in wrong place
    [20_M4 _T_Nut.stl]
2016-04-28 Adding mount for MKS Base board
    [1_MKS_Base_Mount.stl, MKS_Base_mount.fcstd]
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2016-04-30 Adding new images and mounts
    [1_Compact_Direct_Drive_Extruder.stl, 1_PSU_Mount_1.stl, 1_PSU_Mount_2.stl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]
2016-04-30 moved old bed holder scad file to correct folder
    [Bed_Holder.scad]
2016-04-30 PSU Mount - moved mounting point
    [1_PSU_Mount_1.stl, 1_PSU_Mount_2.stl, PSU_Mount.fcstd]
2016-05-01 removing old SCAD PSU mounts
    [PSU-A.scad, PSU-B.scad]
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2016-05-04 moving Bed standoff to test files
    [12_Corner_Bracket_Culain.stl, 1_Bed_Holder_Left.stl, 1_Bed_Holder_Right.stl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]
2016-05-04 moving to correct folder
    [Nyloc-nut-M3.step]
2016-05-04 adding FreeCAD version of foot
    [foot.fcstd]
2016-05-06 brackets in wrong folder
    [12_Corner_Bracket_Culain.stl]
2016-05-08 Carriage updated to new Freecad version
    [1_Carriage.stl, 1_Carriage_clamp.stl]
2016-05-08 Spool clamp Smoothed off for easier removal from bed
    [1_Spool_Clamp_Frame.stl, 1_Spool_Clamp_Outer.stl, Spool_Clamp.fcstd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]
2016-05-08 Foot Freecad file in wrong folder
    [foot.fcstd]
2016-05-09 adding missing reference files
    [Left_Bed_Holder_NEW.stl, left_bed_holder_clamp.scad]
2016-05-10 Adding Test files for Z Axis using 12mm rods
    [12mm_Bed_Carrier.fcstd, 12mm_Bed_Carrier_Left.stl]
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2016-05-10 RRD Mount bracket modified to work with case (to be pushed)
    [1_RRD_Mounting_Bracket_Left_FB2020.stl, 1_RRD_Mounting_Bracket_Right_FB2020.stl]
2016-05-10 slight change to model
    [1_Spool_Clamp_Frame.stl]
2016-05-10 recovery from FreeCad Crash
    [12mm_Bed_Carrier.fcstd]
2016-05-10 Adding 12mm Rod Mount Model
    [12mm_Z_Rod_Holder.fcstd]
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2016-05-10 reducing number of printed T nuts
    [10_M4_T_Nut.stl]
2016-05-10 Adding 12mm Z Rod holder
    [12mm_Z_Rod_Holder.stl]
2016-05-11 Correcting hole size on tab
    [4_Corner_Brace_Mount.stl, 4_Corner_Brace_Mount_Culain.stl]
2016-05-11 adding IGES files - request
    [12mm_Bed_Carrier.iges, 12mm_Z_Rod_Holder.iges, Carriage.iges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]
2016-05-11 Z Endstop tidied up and strengthened
    [1_Z_Endstop.stl, Z_Endstop.fcstd, Z_Endstop.iges]
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2016-05-12 Bottom Corner Brackets Re-Designed#
    [4_Alternate Bottom Bracket_Culain.stl, 4_Bottom_Corner_Bracket.stl, Bottom _Corner_Bracket.fcstd]
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2016-05-13 retiring printed coupler in favour of a rigid coupler
    [2_FB2020_Coupler.stl]
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2016-05-16 Orientating correctly
    [1_Carrier_Left.stl, 1_Carrier_Right.stl]
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2016-05-18 Removing Front Bed Tie
    part is no longer used due to 3 point levelling.
    [1_Front_Bed_Tie.stl]
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2016-05-20 Convert Z Axis to use 12mm Rods
    Z Axis now uses 12mm Smooth rods for extra stability.
    [12mm_Bed_Carrier_Left.stl, 12mm_Z_Rod_Holder.stl, 1_12mm_Bed_Carrier_Left.stl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]
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2016-05-20 Z Rod Holder - added 0.1mm Tolerance
    [12mm_Z_Rod_Holder.fcstd, 4_12mm_Z_Rod_Holder.stl]
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2016-05-23 RAMPS Enclosure Redesigned.
    Added Reset button and extra height to allow for LCD header.
    [RAMPS_Box_Base.stl, RAMPS_Box_Lid.stl, RAMPS_Box_Reset_Button.stl]
2016-05-23 Moving RAMPS box CAD to correct folder
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2016-05-24 Adding RAMPS Enclosure to main files, moved old mount to old files
    RAMPS mount now obsolete, Superseeded by the RAMPS Enclosure.
    [1_RAMPS_Box_Base.stl, 1_RAMPS_Box_Lid.stl, 1_RAMPS_Box_Reset_Button.stl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]
2016-05-24 Adding 30mm Fan Guard for E3D heatsink fan
    [1_30mm_Fan_Guard.stl, 30mm Fan Guard.fcstd]
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2016-05-24 Save from FreeCAD Crash
    [Rod_Clamp.fcstd]
2016-05-26 Y Rod Holders modified to allow for Pan head bolts - name updated
    Y Rod holders renamed from Rod_Clamp* to Rod_Holder* for clarity. Removed excess on model stopping Pan head bolts being used.
    [1_Rod_Clamp_Endstop.stl, 1_Rod_Clamp_Right_Idler.stl, 1_Rod_Holder_Endstop.stl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]
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2016-05-28 Correcting Orientation
    [1_RAMPS_Box_Base.stl]
2016-05-28 Correcting orentation
    [1_RAMPS_Box_Lid.stl]
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2016-06-09 Shortened holder, added extra material to stop wobble
    [Webcam_Holder.fcstd, Webcam_holder.stl]
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2016-06-13 Outer spool clamp changed to use a 608ZZ bearing
    [1_Spool_Clamp_Outer.stl, Spool_Clamp_outer.fcstd]
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2016-06-14 Outer Spool clamp changed to use 608ZZ Bearing
    [Spool_Clamp_outer.fcstd]
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2016-06-14 Correcting Orientation of 400w PSU Mount
    [2_PSU_Mount_S-400-12.stl]
2016-06-14 New Version of Webcam holder for Logitech C270
    [Webcam_Holder.fcstd, Webcam_Mount_C270.fcstd, Webcam_holder.stl]
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2016-08-10 Adding Z Strain relief holes
    Added holes for a cable tie for strain relief on the Z axis
    [12mm_Bed_Carrier.fcstd, 1_12mm_Bed_Carrier_Left.stl, 1_12mm_Bed_Carrier_Right.stl]
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2016-11-06 Updated Small Fan Duct
    Small Fan Duct for E3D redesigned in FreeCAD. Added 0.5mm wall thickness to avoid snapping.
    [1_E3D_duct_small.stl, E3D_Fan_Duct_Small.fcstd, FB2020_Flexi_foot.fcstd]
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2016-11-06 Drawings for Acrylic Side & Back panels for Standard FB2020
    [Back_Panel_FB2020.dxf, Side_Panel_FB2020.dxf]
2016-11-06 Bowden Tube Wire Clip Modified
    Increased wire bundle size to 8mm
    [6_Bowden_Tube_Wire_Clip.stl]
2016-11-06 Test Flexi sound dampening foot
    To be printed in Flexible material
    [Flexi_Foot.stl]
2016-11-06 Test Spring mount For Extuder to stop the spring moving
    [Extruder_Spring_holder.fcstd]
2016-11-07 Small tweaks to Smal Fan duct
    Extended by 1mm, made hanger lug bigger
    [1_E3D_duct_small.stl, E3D_Fan_Duct_Small.fcstd]
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2016-11-20 Quick redesign of Z Endstop
    Added 3mm width, shortened adjustment holes
    [1_Z_Endstop.stl, Z Endstop.fcstd, Z_Endstop.scad]
2016-11-20 Spool holder modified to allow for 3mm Acrylic cladding
    [1_Spool_Rod_Holder_Acrylic.stl, 2_Spool_Clamp.stl, Spool_Holder.fcstd]
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2017-01-05 Spring Holder for Extruder moved to main files
    [1_Extruder_Spring_Holder.stl, Extruder_Spring_holder.fcstd]
2017-01-05 Knob For RRD - 2 versions long and short
    [1_RRD_Knob.stl, 1_RRD_Knob_15mm.stl, RRD_Knob.fcstd]
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2017-01-05 Move Old CAD files to correct folder
    [1_Rod_Holder_Endstop.stl, 1_Rod_Holder_Right_Idler.stl, 2_Rod_Holder.stl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]
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2017-01-05 Edit of Endstop holder to allow for pins on Endstop Board
    [1_Y_Endstop_Holder.stl]
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2017-01-13 Updated Y Rod Holders to stop flexing.
    [2_Y_Rod_Holder_Left.stl, 2_Y_Rod_Holder_Right.stl, Y_Rod_Holder.fcstd]
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2017-02-15 Added fan duct to allow mounting of SN-04 Proximity sensor
    [E3D_Duct_Small-SN04_Mount.stl, E3D_Fan_Duct_Small.fcstd]
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2017-03-08 Lower Y rods by 4mm - combine into one part
    [2_Y_Rod_Holder_Left.stl, 2_Y_Rod_Holder_Right.stl, 4_Y_Rod_Holder.stl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]
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2017-03-14 Remove Schlotzz Extruder - Add Drakon as Submodule
    [1_Compact_Direct_Drive_Extruder_Idler.stl, 1_Compact_Direct_Drive_Extruder_M4.stl]
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2018-06-16 Add new alternative Carriage for the E3D Threaded Heatsink
    [1_Carriage_E3D_Threaded_Heatsink.stl, Carriage_v2.1.fcstd]
2018-06-16 Add Spool Hanger for use with 3mm Perspex sheets
    [Spool_Hanger_Cladding.fcstd]
2018-06-16 Add Small magnetic fan duct to enable auto levelling
    6mm diameter disc magnets for removable probe
    [E3D_Fan_Duct_Small_Auto_level.fcstd]
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2019-03-15 Rework Lead Screw Nut Holder - was not concentric with motor
    [1_Z_Leadscrew_Nut_Holder.stl]
2019-03-26 Leadscrew Nut Mount Out of alignment - Corrected
    [1_Z_Leadscrew_Nut_Mount.stl]
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

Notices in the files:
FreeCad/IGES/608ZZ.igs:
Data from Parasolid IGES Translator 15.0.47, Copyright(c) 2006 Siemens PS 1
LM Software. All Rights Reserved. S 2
